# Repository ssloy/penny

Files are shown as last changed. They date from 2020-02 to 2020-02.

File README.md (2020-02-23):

# Meet Penny#3, a 3 servo hexapod.
Penny is a low budget (roughly ten bucks) hexapod. It can be a great one-weekend project to entertain yourself and your kids. Check for Penny dancing to funky music (youtube link):

Penny dances (https://youtu.be/quMe5CEoOok)

Penny avoids obstacles (youtube link):

Penny dances (https://youtu.be/f4vZZBQZLEU)

In her current state, Penny only knows to walk; she can see (measure distance to) nearby obstacles. Her brains, however, are powerful enough to digest data from many other sensors, send me your suggestions!

Penny is a tremendous fun!

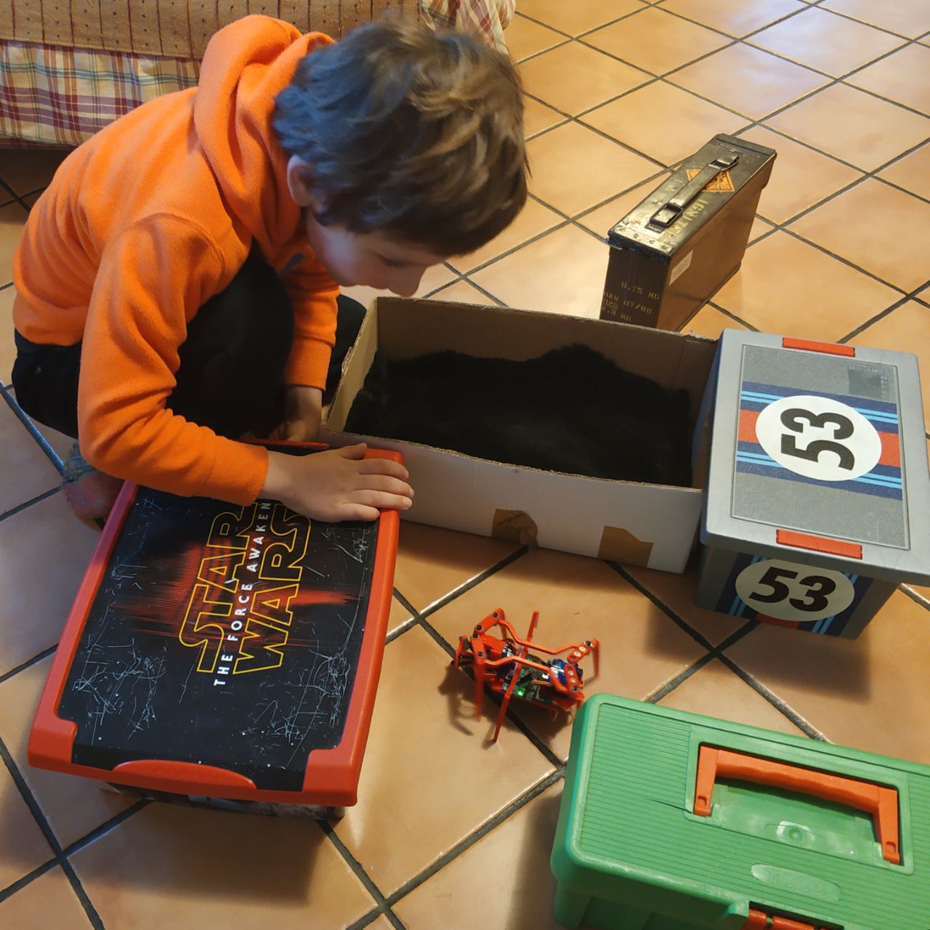
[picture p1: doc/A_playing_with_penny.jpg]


## Credits
Penny has two elder sisters, [Penny](https://youtu.be/7Py03SH5DbE) and [Penny](https://youtu.be/PiVTC8JhZTQ). Note that I have no hardware contributions, all I did is to gather the information, assemble things and write the firmware. I want this wonderful robot to be easy to clone, therefore I created this repository. The original Penny#1 is created by [Jeremy Zimmer](https://www.robotshop.com/community/robots/show/penny). The wiring being cumbersome and cheapduino being discontinued, Dennis van Elteren has designed the motherboard that I also use. Thus Penny#2 was born. Here I present you Penny#3. While I have Dennis' sanction to publish his files, I failed to contact Jeremy. The software, however is distributed under the DO WHAT THE FUCK YOU WANT TO PUBLIC LICENSE.

# How to clone
## Bill of materials
Printing the body costs next to nothing if you have a 3d printer. Here are the main things you need to build the bot:
* The motherboard. You can either etch it by yourself, or you can check chinese factories, any normal day it costs ~10€ / 10 pcs (shipping included). Since the board is tiny, personally I appended it to another order, and it was free of charge for me. You can find an alternative like cheapduino or similar, because the schematics is very, very basic.
* [SG90 9G micro servo, 3 * 1.47€ / piece](https://www.aliexpress.com/item/4000595327297.html)
* [4x AAA battery holder, 1.34€ / piece](https://www.aliexpress.com/item/33049875634.html)
* [ATMega8A-AU (QFP-32), 1€ / piece](https://www.aliexpress.com/item/32557093316.html)
* [IR LED + IR phototransistor, 0.20€ / pair](https://www.aliexpress.com/item/32849824664.html)
* [Electrolytic capacitor 1000uF 16V, 0.17€ / piece](https://www.aliexpress.com/item/32954075821.html)
* [2n3904 transistor, 3 * 0.01€ / piece](https://www.aliexpress.com/item/32494899564.html)
* You will need wires, heat shrink, screws, pin headers, few 0805 resistors and capacitors. All electronic components are listed in the [hardware/motherboard/BOM.html](https://github.com/ssloy/penny/blob/master/hardware/motherboard/BOM.html) file.

**NB:** When bying 9g servos, do not forget that they come in different sizes, Penny is designed for the low profile plastic gears servos. It will work with other servos, but you might need to update SketchUp files for it. Moreover, metal gears are an overkill here.

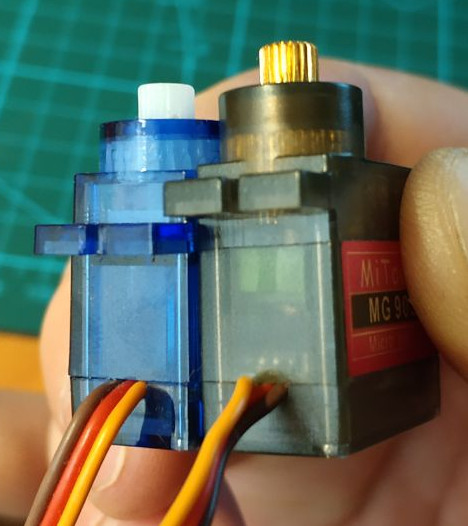
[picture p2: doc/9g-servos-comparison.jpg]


## The body
It is quite straightforward, if you have a printer, just print it. You can find the files in the [hardware/body/](https://github.com/ssloy/penny/tree/master/hardware/body) folder. All the body parts are shown here:

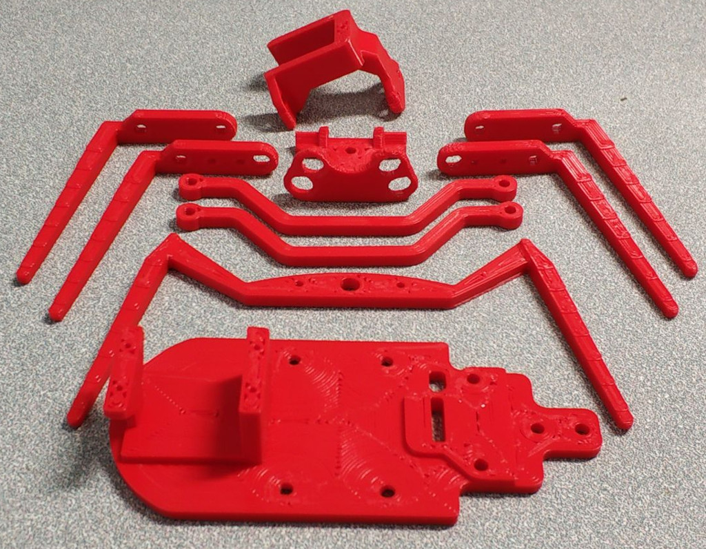
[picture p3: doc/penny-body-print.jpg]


My printer is equipped with a 1mm nozzle, so the prints were completed in less than two hours. When assembled, it should look like this beast:
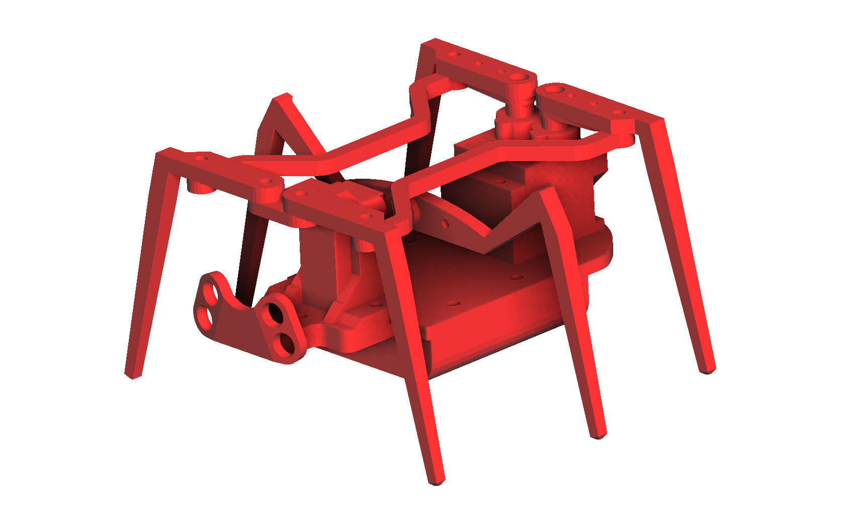
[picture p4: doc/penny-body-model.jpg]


M3 nylon screws are perfect for the assembly. Use nylon washers between moving parts and lock the nut by the method of your choice.
Personally I have locked the thread with a soldering iron:

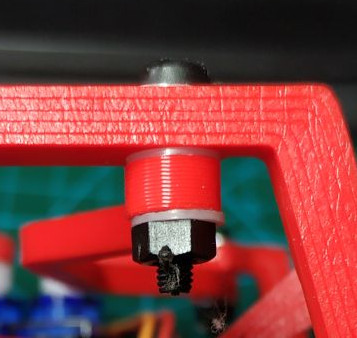
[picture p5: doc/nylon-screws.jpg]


## The motherboard
### The brain
The motherboard itself is pretty basic. It has an ATMega8 microcontroller and the proximity sensor circuit, nothing else. The source files, the gerber files and the bill of materials can be found in the [hardware/motherboard/](https://github.com/ssloy/penny/tree/master/hardware/motherboard) folder. Here is a render of the gerber files:

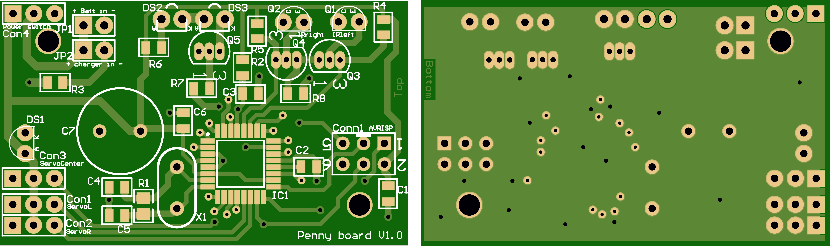
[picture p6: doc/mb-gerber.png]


And the part of the schematics with the brain:

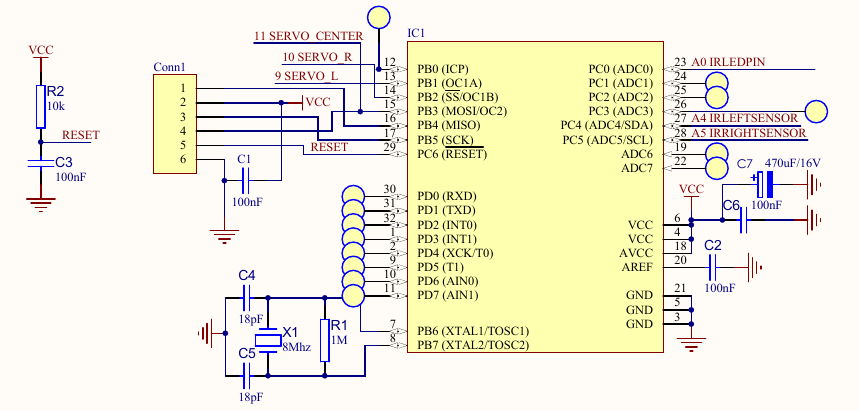
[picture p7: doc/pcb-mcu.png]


I recommend to solder the bare minimum to power up the processor, and to flash it to be sure that nothing is wrong with the delicate soldering. At this stage the motherboard looks like this:

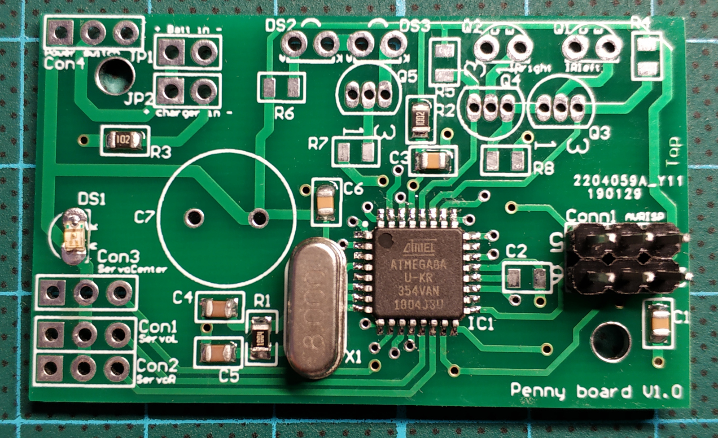
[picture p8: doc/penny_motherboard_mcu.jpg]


**N.B. ATMega8A datasheet specifies its operating voltage at 2.7-5.5V and absolute maximum 6V rating.
A safe option is to power Penny with 4 NiMH 1.2V rechargeable batteries,
but I tried to run Penny with 4 standard alcaline batteries (6.4V in total) and it did not fry the brain.
If you are going this way, I did warn you. It is at your own risk!**

Here is a photo of the motherboard fully populated (with an exception of IR led/phototransistors):

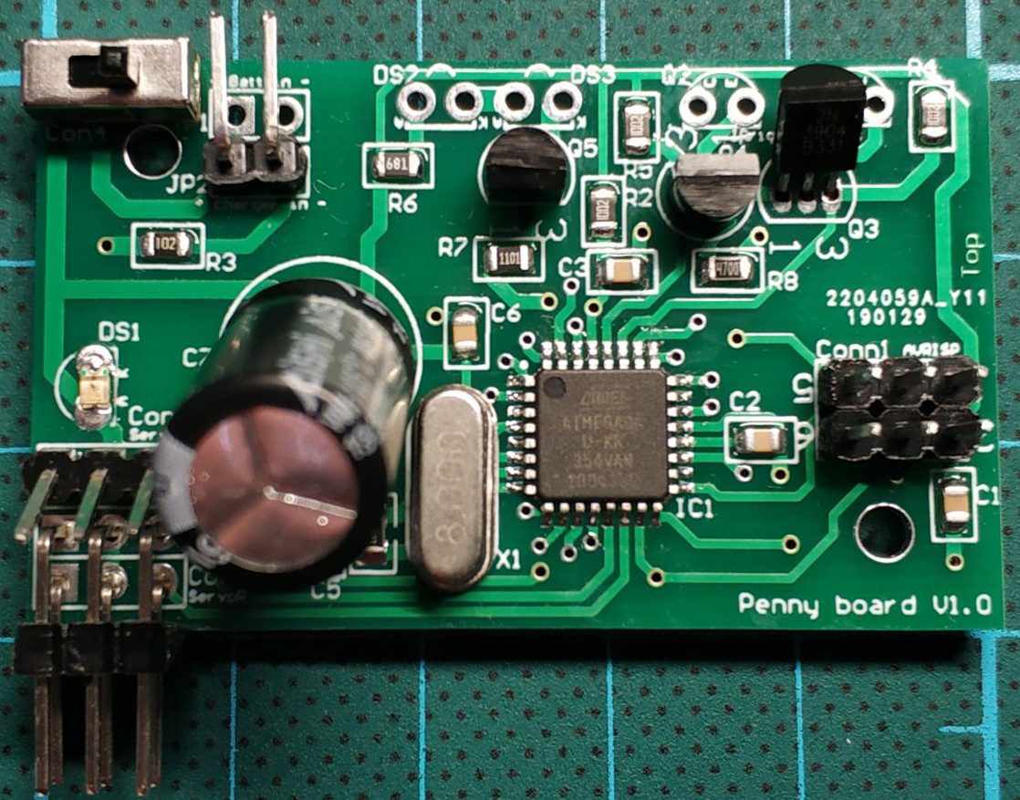
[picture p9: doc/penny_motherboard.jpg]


### The proximity sensor
Penny has two eyes, each one is made of an infrared LED and a corresponding phototransistor.
The LED emits infrared light; this light propagates through the air and once it hits an object it is reflected back towards the phototransistor.
If the object is close, the reflected light will be stronger than if the object is further away.
Note that while the infrared light is not visible by a human eye, some cameras may see it and show it on the recordings,
it can be a handy tool for debugging Penny:



The schematics is very simple:

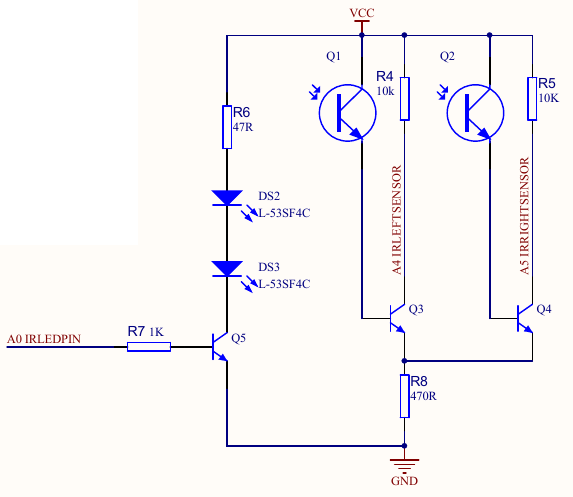
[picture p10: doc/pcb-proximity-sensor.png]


We power up two LEDs, when the phototransistors are not lit, the collector pins of Q3 and Q4 are tied to Vcc, and if the phototransistors
sense the light, the voltage on the collector pins will go down.
Here is the circuit test before I have installed it in the Penny's eyesockets:



Note that you may need to adjust the R6 resistor value.
47 Ohms provides 55mA to the LEDs; some leds might need more or less current.
For example, I have scraped a couple of LEDs from a broken toy, and they work perfectly on 3mA (910 Ohms)!

I recommend to assemble first the sensing unit on a breadboard without the LEDs.
Then light up the LED with a CR2032 or a similar battery, pand put it against the phototransistor (I do not know the internal resistance of the battery, but I have never seen a LED fried from such an operation. Correct me if I am wrong).
Verify that the voltage on the Q3 and Q4 collector pins drops as expected.
Once the sensing unit is okay, try to find a good resistor value for the LEDs to obtain the behaivour you see on the above video.
Note that it is important to put a heatshrink around both the LEDs and the phototransistors to cut off parasitic lights.
Moreover, with heatshrink it fits neatly into the eyesockets. When soldering the 2n3904, I recommend to solder first the center pin, and only then the side pins, otherwise it is too easy to create hard-to-remove solder bridges. Personally I find these little basterds harder to solder than the microcontroller itself (but I am bad at soldering!).

If you do to not have an oscilloscope, that is okay, you can do it with a couple of debugging LEDs, check the blue LEDs on the following video:



For more distant obstacles the LEDs will be less bright.

If you fail to assemble the proximity sensor, or simply dislike it, there are plenty of options:

* You can use isf471 instead of the phototransistors and all the 2n3904 circuitry.
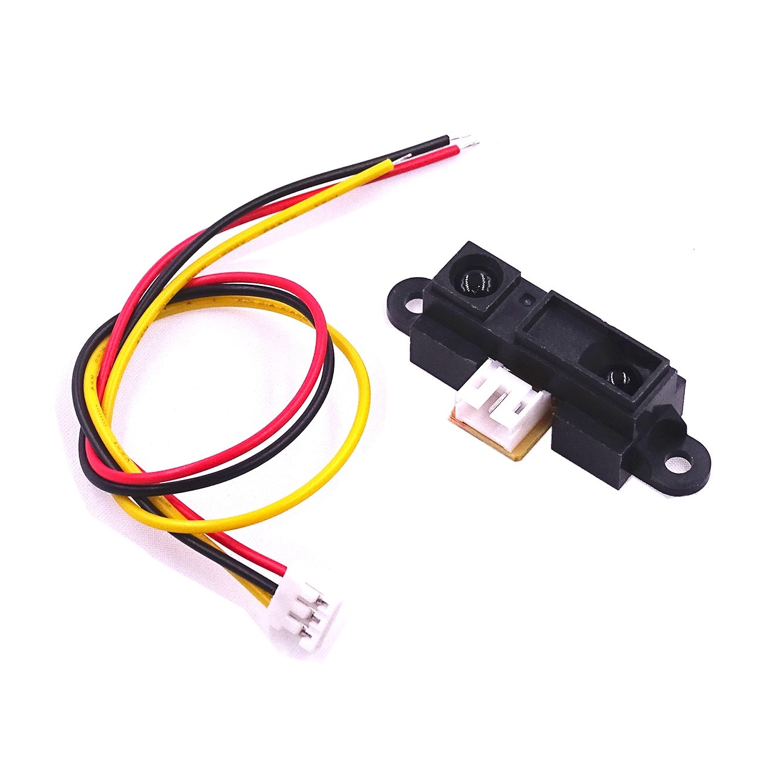
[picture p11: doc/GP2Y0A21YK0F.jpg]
* You can buy Sharp GP2Y0A21YK0F distance measuring units: <br/> 
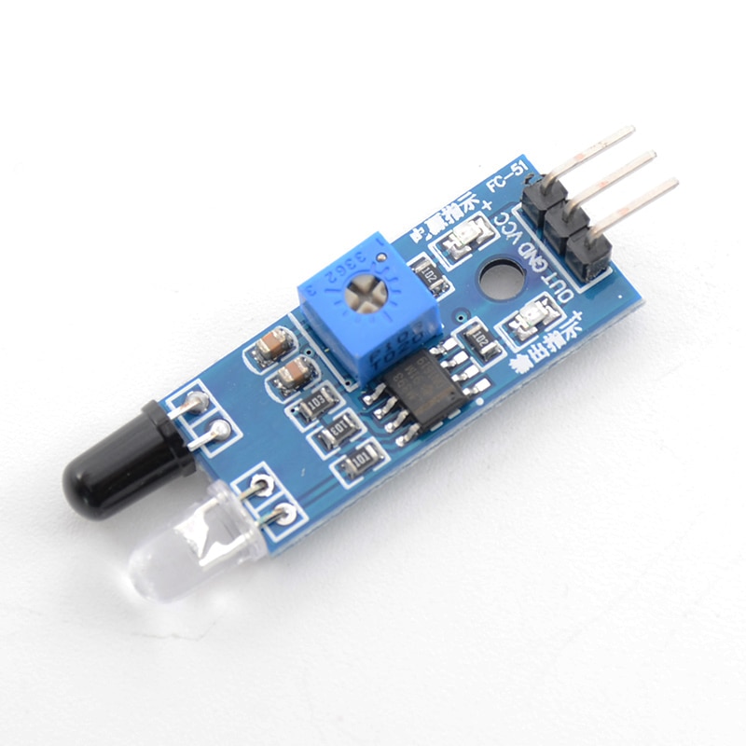
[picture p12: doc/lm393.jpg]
* Or a basic binary proximity sensor based on a LM393 differential comparator: <br/> 

# Firmware explained
Penny can be programmed via arduino environment, but I find it quite obscure for such simple microcontrollers as ATMega8. Let us split the firmware comments into four parts: 
* [how to get the PWM working](https://github.com/ssloy/penny#pwm-generation)
* [how Penny moves legs](https://github.com/ssloy/penny#movement-planner)
* [gait sequences](https://github.com/ssloy/penny#gait-sequences)
* [obstacle avoidance strategy](https://github.com/ssloy/penny#obstacle-detection)

### PWM generation
The servos take a 50 Hz PWM signal; 1 ms minimum pulse width (0 deg), 2 ms maximum pulse width (90 deg). Penny has three servos, two of them are attached to a 16 bit timer (timer1), and the third one to a 8 bit timer (timer2). If I am not mistaken, arduino's Servo.h controls servomotors via software PWM, and I dislike that, therefore both timers are ticking in fast PWM mode.

The microcontroller ticks at 8 MHz, and the timer1 ticks at 1 MHz (prescaler 8), and ICR1 provides the TOP value (20000), thus it restarts every 20 ms, providing a correct 50 Hz signal. OCR1A and OCR1B registers control microsecond pulse widths for the left and right servos.

The problem comes with the center servo attached to a 8 bit timer2. It does not have a handy ICR1 analog, so the overflowing frequency is controlled via the prescaler only. There are no prescalers to approximate 50 Hz well enough, so here is an idea that lies somewhere inbetween a software and a hardware PWM:
* we set timer2 to tick at prescaler 128, thus it overflows after 4.096 ms = 256 * 128/(8 * 10^6).
* At the overflow we disable the timer2, so it is a one-shot pulse.
* At the timer1 capture interrupt we re-arm the (one-shot) timer2.

4 ms is superior to a 2 ms max pulse width we need to control, and is well inferior to the 20 ms re-arming beat. To sum up, let us say we want to put all three servos to the middle position (1500 μs pulse width). We need to do the following:
```c
OCR1A = 1500;    // left servo
OCR1B = 1500;    // right servo
OCR2  = 1500/16; // center servo
```
### Movement planner

First of all, there are 6 important constants in the code:
```c
const uint8_t  zero[3] = {45, 50, 40};     // zero position of the servo (degrees)
const uint8_t range[3] = {25, 25, 20};     // the servos are allowed to move in the zero[i] +- range[i] interval
```
The `zero[3]` array provides the angles of all three servos corresponding to the neutral stance (left image below). Ideally, these angles are to be at 45° (midpoint of the servo range), but in practice if we set the servos to 45°, the legs won't be aligned due to descreet teeth position on the shaft. Next, `range[3]` specifies the admissible range. It means that the servo `i` is allowed to move in the `zero[i]-range[i]`to `zero[i]+range[i]` interval. 

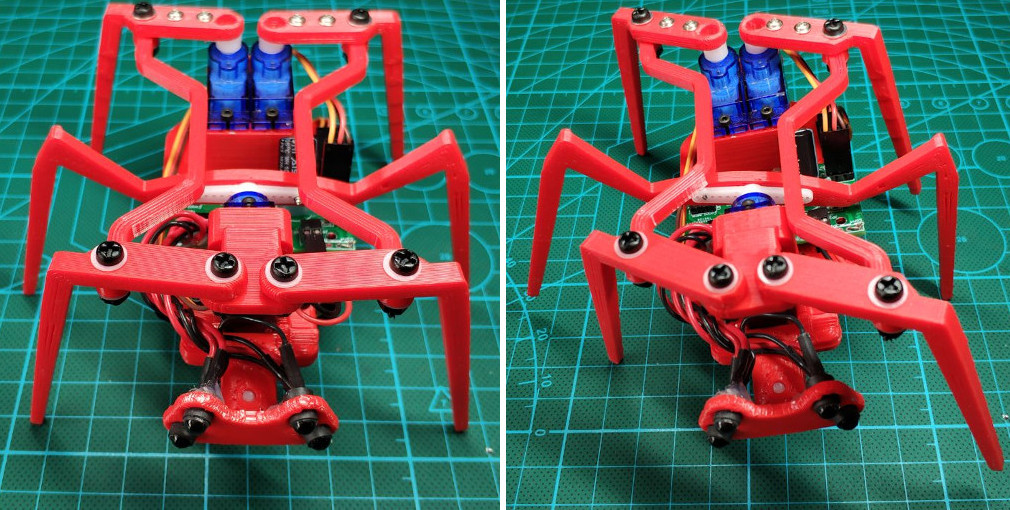
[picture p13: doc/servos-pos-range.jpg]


Current servo position (in degrees, 0°-90°) is supposed to be stored in the `uint8_t pos[3]` array. When calling `update_servo_timers()`, the timers are updated according to the array. The right image above corresponds to the `pos[i]=zero[i]+range[i]` for all three `i=0,1,2`.

All the movements are planned as constant speed. There are four auxiliary arrays for the movement planner: `pos_beg[3], pos_end[3], time_start[3]` and `duration[3]`. Let us suppose that we want to move the left servo only. All we need to do is:
* copy `pos[0]` to `pos_beg[0]`, it marks the starting point of the movement;
* set `pos_end[0]` to the desired position (still in degrees);
* set `time_start[0]` to the current timestamp (milliseconds since the boot);
* and, finally, set `duration[0]` (in seconds). That is, the speed will be `(pos_end[0]-pos_beg[0])/duration[0]` degrees/sec.

Then in an endless loop I invoke `movement_planner()`, it sets the goal `pos[]` according to the plan, and `update_servo_timers()` to update the PWM generator according to the `pos[]` position.

### Gait sequences
Note that all movement planner variables are stored in 3-element arrays, thus the movements (including the speeds) can be independent one from another. 
Despite that, my current gait implementation uses synchronized movements of all three servos.
Let us see how Penny goes forward. To advance, Penny repeats in a loop 4 steps.
All 4 steps are linear movements to following goal positions:
* step 1: `{zero[0]-range[0], zero[1]-range[1], zero[2]+range[2]}`
* step 2: `{zero[0]-range[0], zero[1]-range[1], zero[2]-range[2]}`
* step 3: `{zero[0]+range[0], zero[1]+range[1], zero[2]-range[2]}`
* step 4: `{zero[0]+range[0], zero[1]+range[1], zero[2]+range[2]}`

We can express that as a 2d array (4 triplets of goal positions):
```c
const int8_t advance_sequence[4][3] = {{-1, -1,  1}, {-1, -1, -1}, { 1,  1, -1}, { 1,  1,  1}};
```
This array tells us that the goal position of the servo `i` at the step `step` is `zero[i] + range[i]*advance_sequence[step][i]`.
Then the following code makes Penny to go forward indefinitely:
```c
    uint8_t step = steps_per_sequence-1; // at the initialization stage the (previous) movement is considered to be complete, thus the next movement will be planned starting from the step 0
    while (1) {
        if (is_movement_finished()) {
            step = (step + 1) % 4; // if previous movement is complete, then perform the next step; this variable loops as 0,1,2,3.
            plan_next_movement(step, advance_sequence); // execute next movement
        }
        movement_planner(); // update the servos position according to the planning
        _delay_ms(1);
    }
```

### Obstacle detection

Recall that our proximity sensor provides a voltage that we read throuh channels 4 and 5 of the ADC. To cut off eventual spikes in the readings (esp. knowing that the servos induce tons of noise), at each loop I update the variables `adc_left_eye` and `adc_right_eye` as a low-pass filter over the ADC readings:
```c
        adc_left_eye  = adc_left_eye *.99 + adc_read(5)*.01; // low-pass filter on the ADC readings
        adc_right_eye = adc_right_eye*.99 + adc_read(4)*.01;
```
The cutoff frequency can be set either by adjusting `_delay_ms()` inside the loop or by changing the `.99` and `1-.99` coefficients in the above code.

The presense of an obstacle is detected by a simple threshold over the ADC readings (recall that C does not have `bool` type so I use `uint8_t` instead):
```c
        uint8_t lobst = adc_left_eye  < distance_threshold; // obstacle on the left?
        uint8_t robst = adc_right_eye < distance_threshold; // obstacle on the right?
```

Then at the end of each step of the current sequence I verify if there is an obstacle present and change the plans accordingly. It is as simple as that!

```c
        if (is_movement_finished()) {
            if (!lobst && !robst) {
                sequence = advance_sequence; // no obstacles => go forward
            } else if (lobst && robst) {
                sequence = retreat_sequence; // obstacles left and right => go backwards
            } else if (lobst && !robst) {
                sequence = turn_right_sequence; // obstacle on the left => turn right
            } else if (!lobst && robst) {
                sequence = turn_left_sequence; // obstacle on the right => turn left
            }
            step = (step + 1) % steps_per_sequence; // if previous movement is complete, then perform the next step
            plan_next_movement(step, sequence); // execute next movement
        }
```

# Wishlist
Any contribution is welcome! Send me your ideas; here is a list of things that I'd like to see improved:

### software:
* Propose me an elegant way to have more natural, life-like movements. Right now it moves by a linear interpolations between keyframes, it would be great if the robot was less shaky. Probably, non-linear interpolation between the same keyframes with pre-computed accelerations?
* Propose new strategies of obstacle detection. Current implementation is very basic and aims a good source code readability rather then WOW robot's behaviour.
* I guess that it would be a good idea to port the code to the arduino environment for those who do not want to call avr-gcc directly (or for those who are afraid of meddling with AVR registers). If you can do it, send me a pull request or fork the repository.

### hardware:
If you are a good soul willing to create a V2 of the motherboard, you are very welcome to do so. Here are the things that I'd like to be fixed/added/modified in the motherboard:
* The main thing is the on/off switch to cut off servo motors power during flashing;
* Remove the crystal, internal RC should be just fine;
* Replace through-hole components by their SMD analogs;
* Replace R6 with a potentiometer to adjust the proximity sensor more easily;
* Propose good (small and foolproof) connectors instead of pin headers and optimize their placement;
* IR LEDs pads are very hard to reach under the center servo. The only viable option with the V1 motherboard is to solder the wires;
* Move a little bit the big capacitor. I had to incline it, otherwise the screw in center legs would destroy it;
* Add test pads easy to access with an oscilloscope;
* Add a couple of debugging LEDs;
* Create good soldering points for unused ATMega8 pins for debugging purposes and further extension.

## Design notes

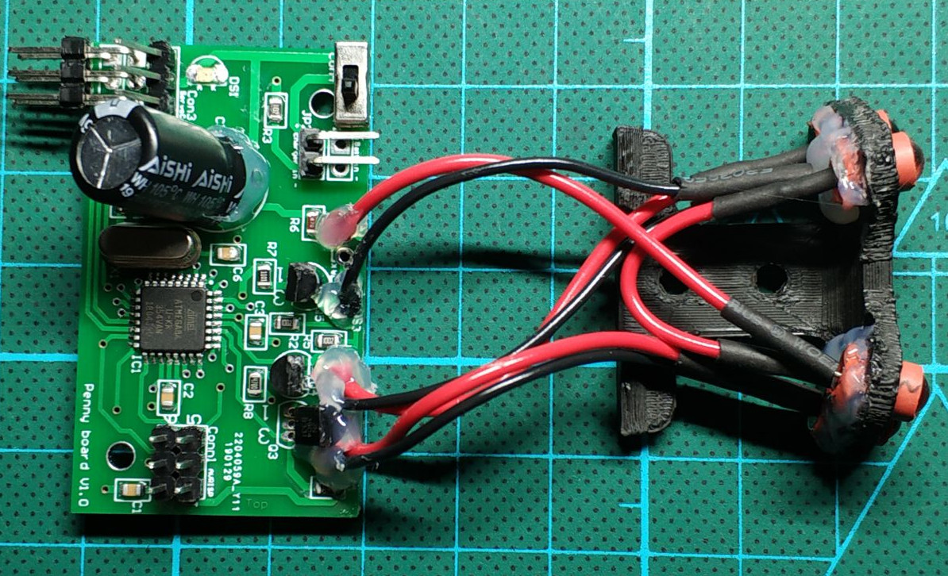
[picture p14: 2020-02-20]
doc/penny_motherboard_with_proximity_sensor.jpg

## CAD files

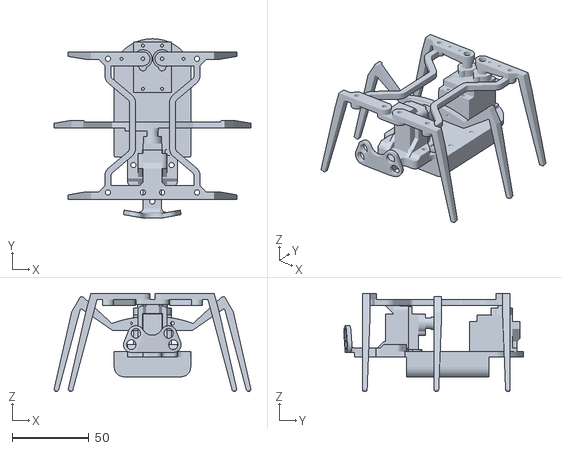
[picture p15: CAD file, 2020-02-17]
hardware/body/3ServoHexapod_Assembled.stl
128.5 x 117.1 x 64.1

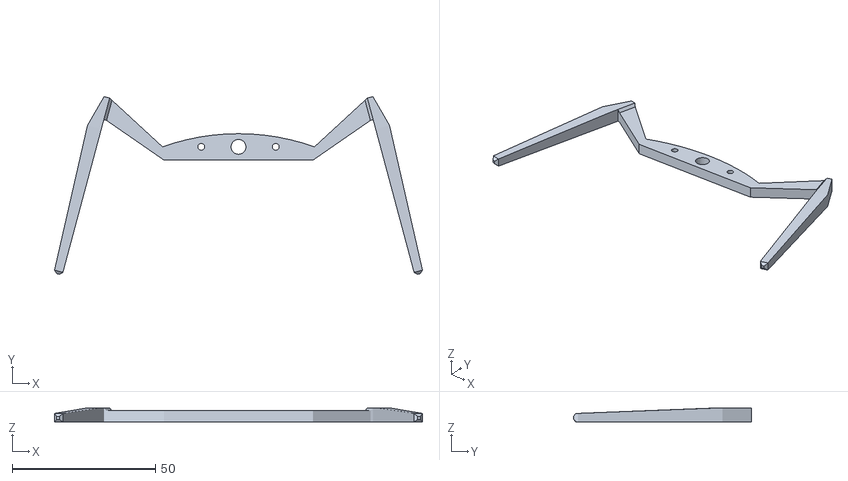
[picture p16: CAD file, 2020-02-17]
hardware/body/CenterLegs.stl
128.5 x 62.1 x 5.00

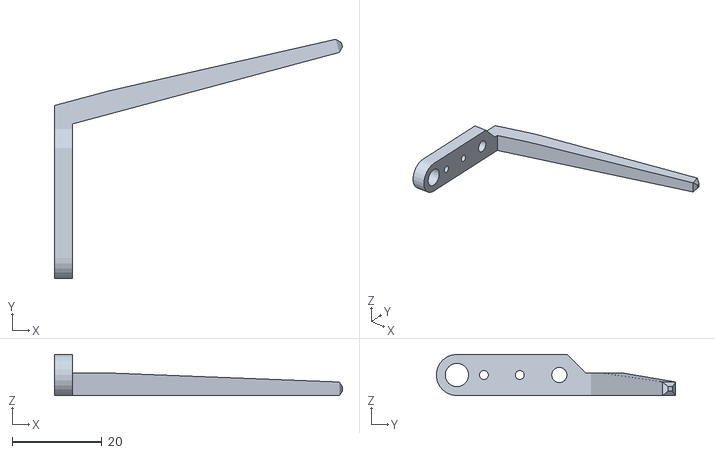
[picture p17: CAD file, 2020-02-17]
hardware/body/BackRightLeg.stl
64.1 x 53.3 x 9.20

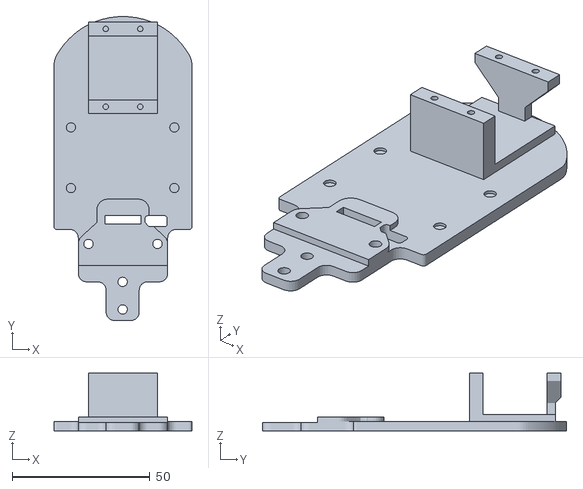
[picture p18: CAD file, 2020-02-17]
hardware/body/Chassis.stl
50.0 x 110.2 x 21.0

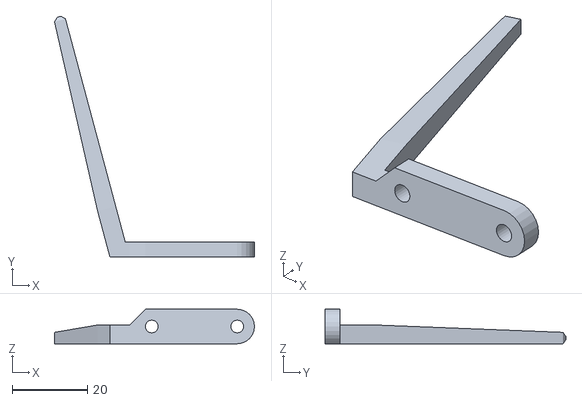
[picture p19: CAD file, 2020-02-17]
hardware/body/FrontRightLeg.stl
53.3 x 64.1 x 9.20

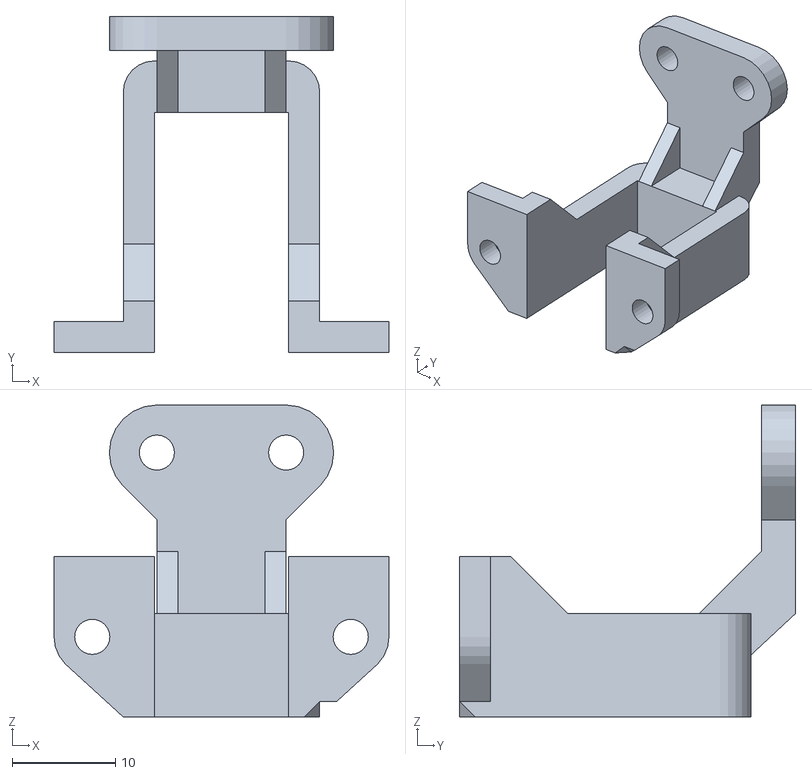
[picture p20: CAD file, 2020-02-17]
hardware/body/FrontServoMount.stl
32.4 x 32.5 x 30.2

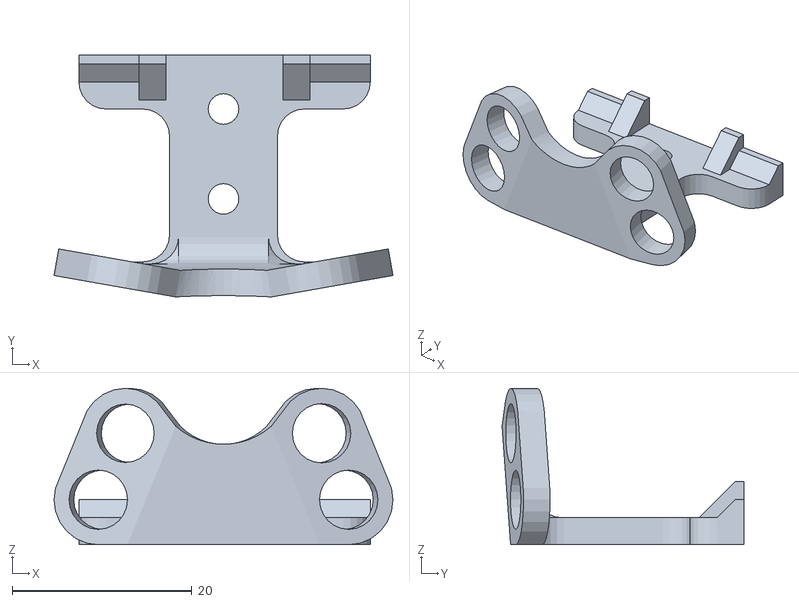
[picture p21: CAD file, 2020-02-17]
hardware/body/Head.stl
37.7 x 26.9 x 17.4

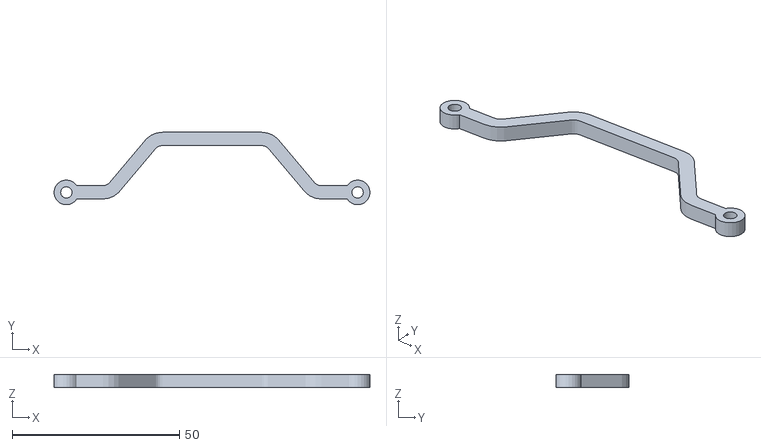
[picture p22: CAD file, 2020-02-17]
hardware/body/LegPushRodFinal.stl
94.6 x 21.7 x 4.00

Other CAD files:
hardware/body/BackLeftLeg.stl
hardware/body/FrontLeftLeg.stl
hardware/body/3ServoHexapod_Assembled.skp
hardware/body/BackLeftLeg.skp
hardware/body/BackRightLeg.skp
hardware/body/CenterLegs.skp
hardware/body/Chassis.skp
hardware/body/FrontLeftLeg.skp
hardware/body/FrontRightLeg.skp
hardware/body/FrontServoMount.skp
hardware/body/Head.skp
hardware/body/LegPushRodFinal.skp

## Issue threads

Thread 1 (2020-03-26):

Penny clone (Arduino-ESP32 based)

sensboston, 2020-03-26:
Finally got my hands on "Penny" last weekend, here is a result: https://www.youtube.com/watch?v=iT2JZWRhM9s

ESP32 dev board a lil-bit wider for original design but it's OK. Will fork project and publish my changes soon, after "polishing" code (I hope so).

P.S. By the way, we've already met on habr. I already received PCBs but not CPUs (from ali, for original design). But I'm thinking about adopt RPi Zero W (got a couple for the sale price, $5 each).

ssloy, 2020-03-26:
Nice job! Personally I'd like to work on the quality of the movements; right now my code produces a rough jerky pace. Ultrasonic sensors can fail to detect foam blocks, as it absorbs sound. I'd suggest to try with regular card boxes. Keep me updated please!

sensboston, 2020-03-26:
> Ultrasonic sensors can fail to detect foam blocks
Thanks, I didn't know that (just picked some of foam specimens I brought from work, for my children), will try today different kind of blocks (children's plastic cubes).

Dmitry (btw, I'm Sergey), could you redesign frame for a little? Make a middle gap wider, legs longer and motor fixtures higher (to provide more space to fit RPi Zero and probably use 4 AA battery holder or RC battery)? Also, have you resolved issue with walking on the hardwood floor (or any other smooth surface)? My "Penny" walks nice on a carpet but fails on hardwood floor. Might be, rubber "shoes" will solve the problem but I need an idea where to get 'em.

ssloy, 2020-03-26:
Different sensors have their flaws, for example, infrared-based:
- cannot work outdoors (blinded by the sun)
- fail to see mirror / glass / black objects
whereas ultrasonic-based:
- work outdoors to some extent, handle mirrors, but fail to see cloth
- must face the walls more or less orthogonally. If the angle is small enough (almost parallel to a wall), the sound bounces off the wall without returning to the receiver.

Note that I have mounted two sensors in order to detect whether the bot has to turn right or left to avoid the obstacle. The repository contains source google sketchup files, those are really easy to adjust to suit your needs.

As for the socks, for the moment I did nothing, but I am all about low budget. The possibilites are:
- bits of rubber hose ([check this photo of my quadruped](https://raw.githubusercontent.com/ssloy/quadruped/master/doc/quadruped.jpg))
- dip it into liquid rubber / silicone rubber

sensboston, 2020-03-26:
> I have mounted two sensors in order to detect whether the bot has to turn right or left to avoid the obstacle.

Yeah, that smart. I ordered a few IR-sensors on ali, as you recommended (that was my mistake but I tried to fit in $10 budget - eBay prices from US sellers are higher 3-4 times) but they haven't arrived yet.

> The repository contains source google sketchup files, those are really easy to adjust to suit your needs.

I do have 0 experience working with google sketchup, but the main problem - I don't have 3D printer (probably, need to purchase good one, as an "entertainment" device). From my understanding, any frame changes (even a simple scaling) will require a test printing, to be sure what everything is OK. Guy from my work, Nelson, printed (for $8) my current Penny parts for me but I can't ask him (especially now, we're mostly working from home) to make a test prints.

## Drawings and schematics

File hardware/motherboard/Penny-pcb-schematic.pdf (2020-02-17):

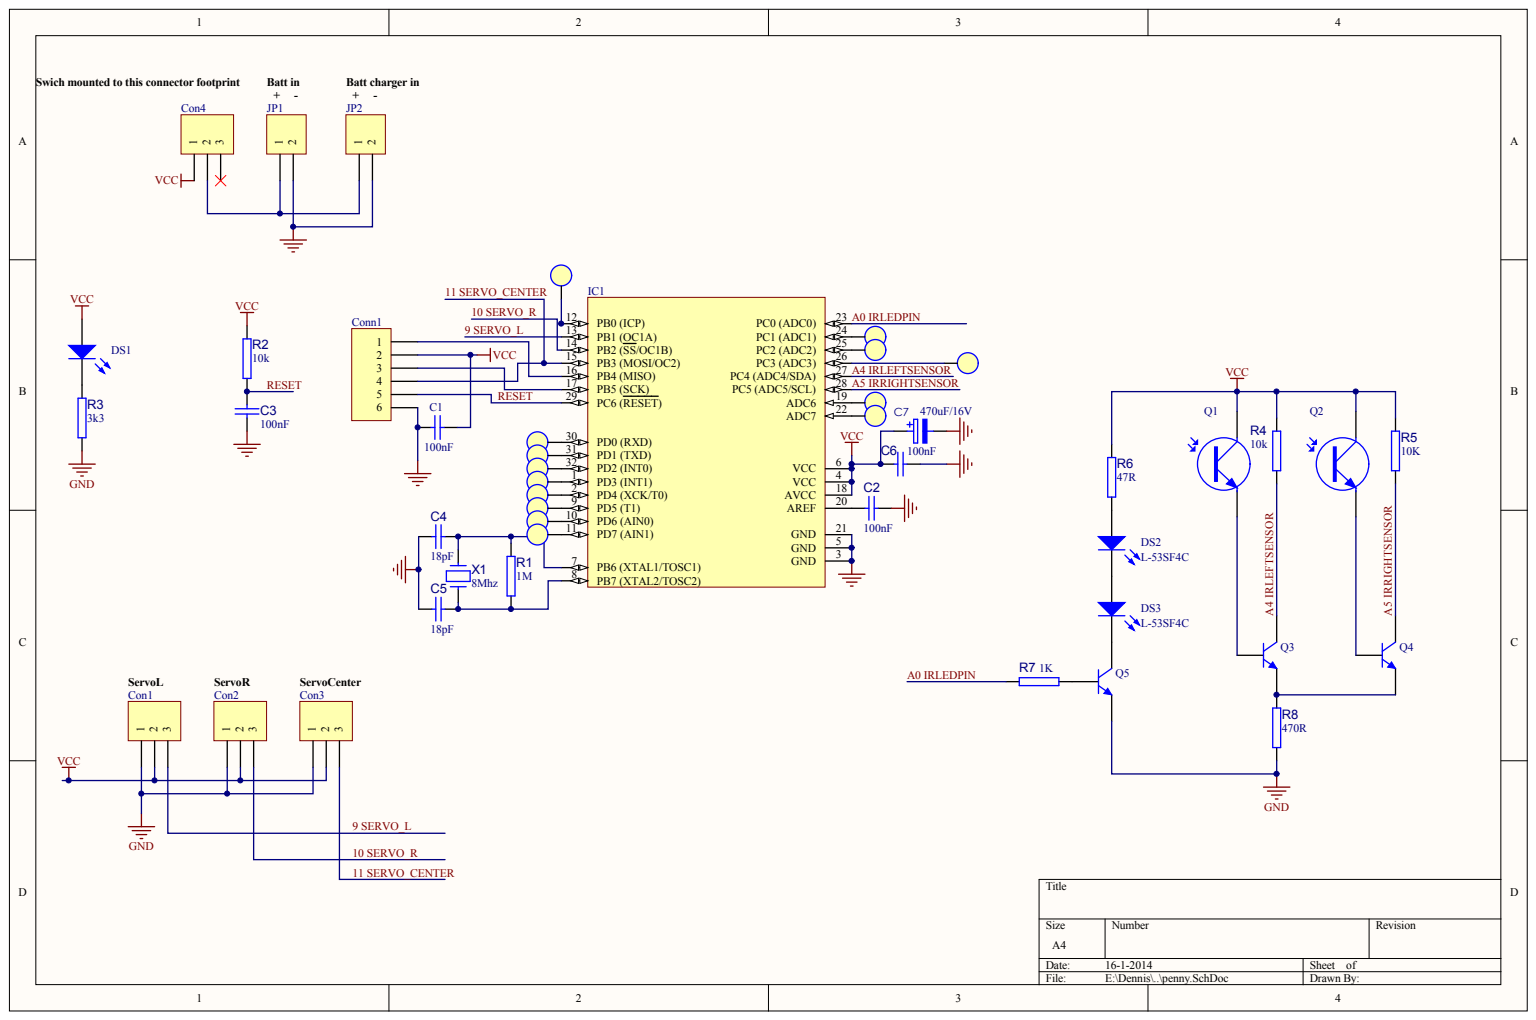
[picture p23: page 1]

Swich mounted to this connector footprint

VCC | PB3 (MOSI/OC2) 15

PB4 (MISO) 16
PB5 (SCK) 17

RESET

PD0 (RXD) 30

9 SERVO_L

10 SERVO_R

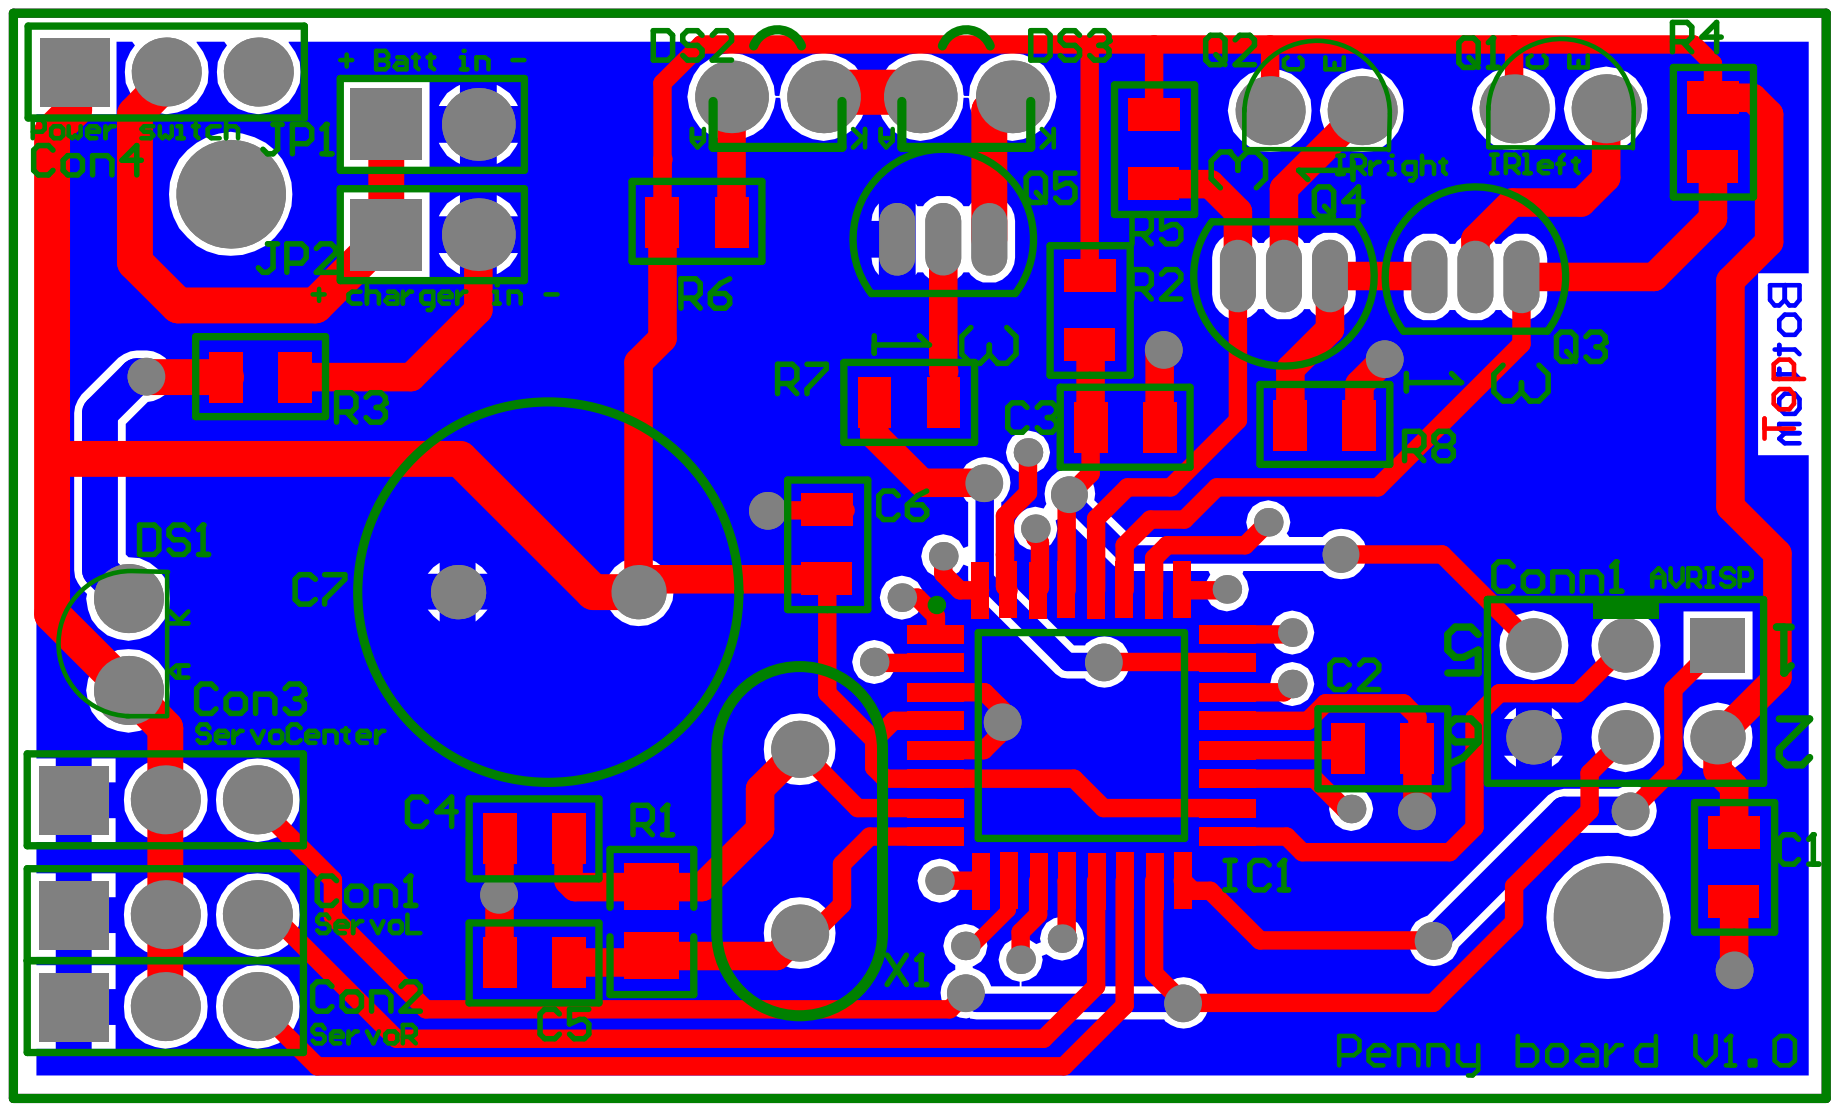
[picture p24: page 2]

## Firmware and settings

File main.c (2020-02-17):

#define F_CPU 8000000L
#include <avr/io.h>
#include <util/delay.h>
#include <avr/interrupt.h>

volatile uint32_t millis = 0; // an approximation of milliseconds elapsed since boot

// these parameters are to tune depending on your actual hardware
const uint8_t  zero[3] = {45, 50, 40};     // zero position of the servo (degrees)
const uint8_t range[3] = {25, 25, 20};     // the servos are allowed to move in the zero[i] +- range[i] interval
const uint16_t distance_threshold = 768;   // ADC threshold for obstacle detection, in principle atmega8 ADC returns [0,1023] values, but the schematics imposes a narrower interval

// movement planner variables
volatile uint8_t     pos[3] = {45, 45, 45};        // current servo position            (degrees)
volatile uint8_t pos_beg[3] = {45, 45, 45};        // starting position for each servo  (degrees)
volatile uint8_t pos_end[3] = {45, 45, 45};        // goal position for each servo      (degrees)
volatile uint32_t time_start[3] = {0, 0, 0};       // beginning of the motion timestamp (milliseconds)
volatile float      duration[3] = {.1f, .1f, .1f}; // movement duration                 (sec)

// gait sequences
const uint8_t steps_per_sequence = 4;                  // each gait is a periodic sequence of 4 steps
const float step_time[4] = {.33f, .166f, .33f, .166f}; // duration of each of 4 steps
const int8_t    advance_sequence[4][3] = {{-1, -1,  1}, {-1, -1, -1}, { 1,  1, -1}, { 1,  1,  1}}; // for each of 4 steps
const int8_t    retreat_sequence[4][3] = {{-1, -1, -1}, {-1, -1,  1}, { 1,  1,  1}, { 1,  1, -1}}; // these numbers determine movement goals,
const int8_t  turn_left_sequence[4][3] = {{ 1, -1,  1}, { 1, -1, -1}, {-1,  1, -1}, {-1,  1,  1}}; // whether we have to add or subtract range[i] from zero[i]
const int8_t turn_right_sequence[4][3] = {{-1,  1,  1}, {-1,  1, -1}, { 1, -1, -1}, { 1, -1,  1}}; // i.e. the goal position of the servo i is zero[i] + range[i]*sequence[step][i]

// The servos take a 50 Hz PWM signal; 1 ms minimum pulse width (0 deg), 2 ms maximum pulse width (90 deg).
// I have three servos, two of them are attached to a 16 bit timer (timer1), and the third one to a 8 bit timer (timer2).
// I dislike software PWM, therefore both timers are ticking in fast PWM mode.
// Timer1 ticks at 1 MHz (prescaler 8), and ICR1 provides the TOP value (20000), thus it restarts every 20 ms, providing a correct 50 Hz signal.
// OCR1A and OCR1B are the microsecond pulse widths for the left and right servos.
//
// The problem comes with the center servo attached to a 8 bit timer2.
// It does not have a handy ICR1 analog, so the overflowing frequency is controlled via the prescaler only.
// There are no prescalers good enough to approximate 50 Hz, here is an idea that lies somewhere between a software and a hardware PWM:
// we set timer2 to tick at prescaler 128, thus it overflows after 4.096 ms = 256*128/(8*10^6).
// At the overflow we disable the timer2, so it is a one shot pulse.
// At the timer1 capture interrupt we re-arm the (one-shot) timer2.
// 4 ms is superior to a 2 ms max pulse width we need to control, and is well inferior to the 20 ms re-arming beat.
// To sum up, let us say we want to put all three servos to the middle position (1.5 ms pulse width).
// We need to do the following:
// left servo:   OCR1A = 1500
// right servo:  OCR1B = 1500
// center servo: OCR2  = 1500/16

void update_servo_timers() {
    OCR1A =  1000 + ((uint16_t)pos[0]*100)/9;     //  left
    OCR1B =  1000 + ((uint16_t)pos[1]*100)/9;     //  right
    OCR2  = (1000 + ((uint16_t)pos[2]*100)/9)/16; //  center
}

inline void init_timer1() {
    TCCR1A = (1<<COM1A1) | (1<<COM1B1) | (1<<WGM11); // fast PWM mode, TOP determined by ICR1 - non-inverting Compare Output mode
    TCCR1B = (1<<WGM13) | (1<<WGM12) | (1<<CS11);    // set prescaler to 8, fast PWM Mode mode continued
    ICR1 = 20000;      // set period to 20 ms
    TCNT1 = 0;         // reset timer
}

inline void init_timer2() {
    TCNT2 = 255;
    TCCR2 = (1<<WGM20) | (1<<WGM21) | (1<<COM21) | (1<<CS22) | (1<<CS20); // prescaler 128, fast PWM mode, clear OC2 on Compare Match, set OC2 at bottom (non-inverting mode)
}

void init_servos() {
    init_timer1();
    init_timer2();
    update_servo_timers();
    TIMSK |= (1<<TICIE1) | (1<<OCIE2); // initialize interrupts, activate
    sei();
}

ISR(TIMER2_COMP_vect) { // overflow interrupt timer2
    TCCR2 = 0; // stop timer2
}

ISR(TIMER1_CAPT_vect) { // capture interrupt timer1
    millis += 20;
    init_timer2();
}

uint16_t adc_read(uint8_t ch) {
    ADMUX = (1<<REFS0) | (ch&7); // AVcc with external capacitor at AREF pin
    ADCSRA = (1<<ADEN) | (1<<ADSC) | (1<<ADPS2) | (1<<ADPS1) | (1<<ADPS0); // ADC enable, start one conversion, set the prescaler to 128 (8000KHz/128 = 62.5KHz)
    while (ADCSRA & (1<<ADSC)); // we have started a single conversion; wait for the conversion to complete
    return ADC;
}

#define MIN(a, b)            (((a) < (b)) ? (a) : (b))
#define MAX(a, b)            (((a) > (b)) ? (a) : (b))
#define CLAMP(x, low, high)  (MIN(MAX((x), (low)), (high)))

// for the given servo, this function returns its current step phase [0.f, 1.f]
inline float movement_phase(uint8_t servo) {
    return CLAMP((millis - time_start[servo])/(1000.f * duration[servo]), 0.f, 1.f);
}

// update PWM servo signals according to the movement planning
inline void movement_planner() {
    for (uint8_t i=0; i<3; i++)
        pos[i] = CLAMP(pos_beg[i] + (pos_end[i] - pos_beg[i])*movement_phase(i), zero[i]-range[i], zero[i]+range[i]);
    update_servo_timers();
}

// copy the step of the sequence to the movement planner variables
inline void plan_next_movement(uint8_t step, int8_t sequence[][3]) {
    for (uint8_t i=0; i<3; i++) {                           // for each of 3 servos
        pos_beg[i] = pos[i];                                // we go from pos_beg[i]
        pos_end[i] = zero[i] + range[i]*sequence[step][i];  // to pos_end[i],
        time_start[i] = millis;                             // the movement is initiated at time_start[i] (right now)
        duration[i] = step_time[step];                      // and should last for step_time[step]
    }
}

// are we done moving?
inline uint8_t is_movement_finished() {
    uint8_t finished = 1;
    for (uint8_t i=0; i<3; i++)
        finished &= (movement_phase(i)>=1.f);
    return finished;
}

// well duh
void go_to_zero_stance() {
    for (uint8_t i=0; i<3; i++) pos[i] = zero[i];
    update_servo_timers();
}

int main(void) {
    DDRC &= ~_BV(4); // input: right phototransistor
    DDRC &= ~_BV(5); // input: left  phototransistor
    DDRC |=  _BV(0); // output: IR LED control
    DDRB |=  _BV(1); // output: left servo
    DDRB |=  _BV(2); // output: right servo
    DDRB |=  _BV(3); // output: center servo
    PORTC |= _BV(0); // set the LED control pin to HIGH
    init_servos();

    go_to_zero_stance();
    _delay_ms(3000);

    int8_t (*sequence)[3] = (int8_t(*)[3])advance_sequence; // by default we go forward
    uint8_t step = steps_per_sequence-1; // at the initialization stage the (previous) movement is considered to be complete, thus the next movement will be planned starting from the step 0

    uint16_t adc_left_eye  = adc_read(5);
    uint16_t adc_right_eye = adc_read(4);
    uint32_t start = millis;
    while (1) {
        adc_left_eye  = adc_left_eye *.99 + adc_read(5)*.01; // low-pass filter on the ADC readings
        adc_right_eye = adc_right_eye*.99 + adc_read(4)*.01;
        uint8_t lobst = adc_left_eye  < distance_threshold; // obstacle on the left?
        uint8_t robst = adc_right_eye < distance_threshold; // obstacle on the right?

        if (is_movement_finished()) {
            if (!lobst && !robst && step==steps_per_sequence-1) { // the obstacles are checked at every step with an exception of go forward decision, it is made at the end of each sequence
                sequence = (int8_t(*)[3])advance_sequence; // no obstacles => go forward
            } else if (lobst && robst) {
                sequence = (int8_t(*)[3])retreat_sequence; // obstacles left and right => go backwards
            } else if (lobst && !robst) {
                sequence = (int8_t(*)[3])turn_right_sequence; // obstacle on the left => turn right
            } else if (!lobst && robst) {
                sequence = (int8_t(*)[3])turn_left_sequence; // obstacle on the right => turn left
            }
            step = (step + 1) % steps_per_sequence; // if previous movement is complete, then perform the next step
            plan_next_movement(step, sequence); // execute next movement
        }
        movement_planner(); // update the servos position according to the planning

        _delay_ms(1);
        if (millis-start>60L*1000L) break; // 60 seconds total running time
    }

    go_to_zero_stance();
    while (1) _delay_ms(10);
    return 0;
}

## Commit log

2020-02-02 penny led blink
2020-02-02 first working servo drive (oc1b)
2020-02-02 left and right servos sweeping (oc1a + oc1b)
2020-02-02 sweeping all three servos
2020-02-02 three servos are controlled, the setup is commented
2020-02-05 working ADC; IR proximity sensor works like a charm
2020-02-09 proximity sensor video
2020-02-09 body print
2020-02-17 hardware: the body and the motherboard
    [3ServoHexapod_Assembled.skp, 3ServoHexapod_Assembled.stl, BackLeftLeg.skp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]
2020-02-18 servos side-by-side
2020-02-19 ir leds video
2020-02-19 plug-n-play sensor images
2020-02-19 power option warning
